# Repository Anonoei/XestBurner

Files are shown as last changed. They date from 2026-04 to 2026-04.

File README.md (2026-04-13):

# XestBurner
A light modular toolhead designed in OpenSCAD

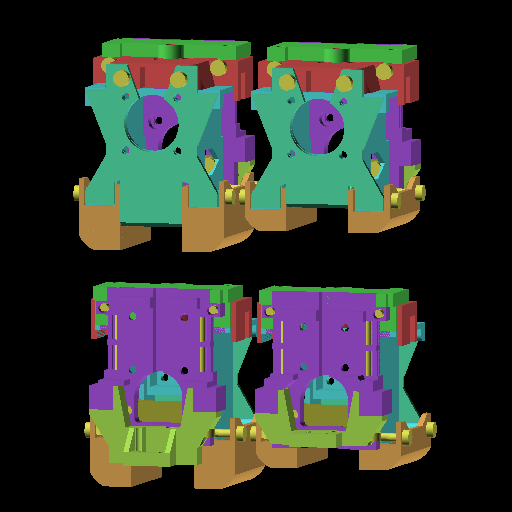
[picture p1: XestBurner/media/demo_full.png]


**This is WORK-IN-PROGRESS**

## Links
- [Description](#description)
- [BOM](#bom)
- [STLs](#stls)
- [Assembly Guide](ASSEMBLY.md)

## Description
XestBurner is meant to be as small as possible, maximizing available print space, while also being modular and allowing components to be switched with minimal tweaks to the toolhead.

XestBurner works with HF (standard, v6) hotends, and UHF (volcano) hotends.

The HF variant measures 61x53x67 (width (x)/depth (y)/height (z)).

### Why?
This toolhead was heavily inspired by the amazing work done for  [Xol](https://github.com/Armchair-Heavy-Industries/Xol-Toolhead), and [Dragonburner](https://github.com/chirpy2605/voron/tree/main/V0/Dragon_Burner)

I switched to a CHUBE hotend, and found that none of the current toolheads supported it, along with features that are necessary, like ease-of-assembly, modular components, and being light.

This toolhead was designed around having a similar footprint to DragonBurner, supporting CHUBE (and other large hotends), and using only M3 hardware.

## BOM
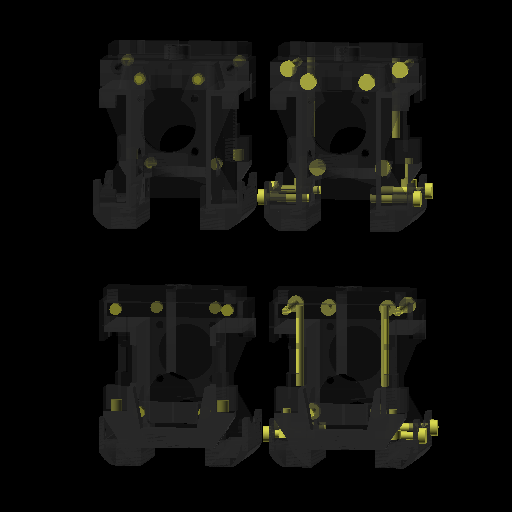
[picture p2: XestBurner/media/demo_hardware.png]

- Prints:
  - Housing
  - Housing Brace
  - Ducts (HF or UHF)
  - [Carriage mount](#carriage)
  - [Hotend mount](#hotend)
  - [Extruder mount](#extruder)
  - [Probe mount](#probe)
  - [Faceplate](#faceplate)
- Hardware:
  - 2x 4010 blower fans (sides of housing)
    - [WINSINN (Amazon)](https://www.amazon.com/WINSINN-Turbine-Brushless-Hydraulic-Extruder/dp/B07L2WTH7H)
    - [West3D BERSERKER VINDR](https://west3d.com/products/berserker-vindr-ulta-performance-4010-blower-fan-24v-4010b-24v-a-40x10mm)
    - [Fabreeko HoneyBadger](https://www.fabreeko.com/products/4010-blower-p-series-fan-by-honeybadger)
    - [KB3D](https://kb-3d.com/store/fans/663-4010-ball-bearing-blower-fan-24v-1662421807065.html)
  - 1x 2510 fan (front of housing)
    - [WINSINN (Amazon)](https://www.amazon.com/WINSINN-Bearings-Brushless-Cooling-25mm10mm/dp/B08R9JXMGP?tag=ustxtaddt-20&th=1)
    - [West3D BERSERKER VINDR](https://west3d.com/products/berserker-vindr-ultra-performance-2510-axial-fan-24v-2510a-24v-a-25x10mm)
    - [Fabreeko HoneyBadger](https://www.fabreeko.com/products/2510-performance-axial-fan-by-honeybadger)
    - [KB3D](https://kb-3d.com/store/fans/3684-2510-ball-bearing-cooling-fan-24v-1740693669311.html)
  - 8x M3x4x5 (Voron) heatsets
    - 6x for carriage, 2 for housing brace, 2 for hotend/extruder, 2 for probe
    - 2x for hotend mount
  - 2x M3x30 pins (inside the carriage for belts)
  - 2x SHCS/BHCS M3x6 (faceplate, into 2x heatsets on the hotend mount)
    - M3x8 probably works
  - 6x SHCS/BHCS M3x8
    - 4x: faceplate, into 2510 fan
    - 2x: probe mount, into 2x heatsets on the bottom of the carriage
  - 4x SHCS M3x16 (housing ducts, through the 4010 fans)
  - 2x SHCS M3x30 (hotend mount, into 2x heatsets on the front of the carriage)
- Variants
  - Carriage
    - MGN12H
      - 4x SHCS M3x8 (?)
    - MGN9H
      - 4x SHCS M3x8 (?)
  - Extruder
    - Sherpa Mini
      - 2x M3x4x5 heatsets
      - 2x SHCS M3x8 (?)
  - Probe
    - Klicky PCB
      - 3x M2.5 heatsets

## STLs
### Base
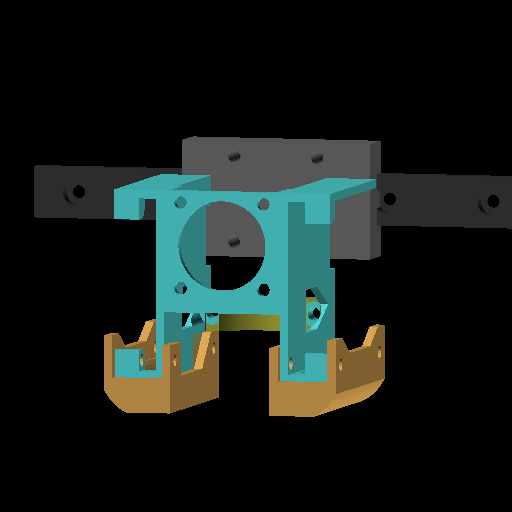
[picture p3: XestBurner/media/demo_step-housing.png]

- [Housing](XestBurner/STLs/XB-housing.stl)
- [Housing: Brace](XestBurner/STLs/XB-housing_brace.stl)
- Ducts:
  - [HF](XestBurner/STLs/XB-ducts-hf.stl)
  - [UHF](XestBurner/STLs/XB-ducts-uhf.stl)

### Carriage
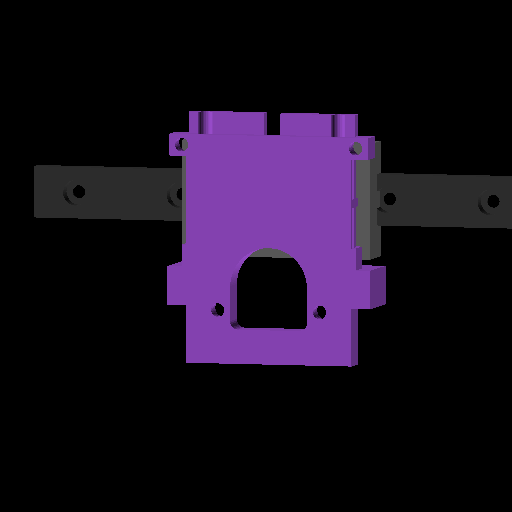
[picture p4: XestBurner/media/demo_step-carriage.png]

- [MGN9H](XestBurner/STLs/XB-carriage_MGN9.stl)
- [MGN12H](XestBurner/STLs/XB-carriage_MGN12.stl)

### Hotend
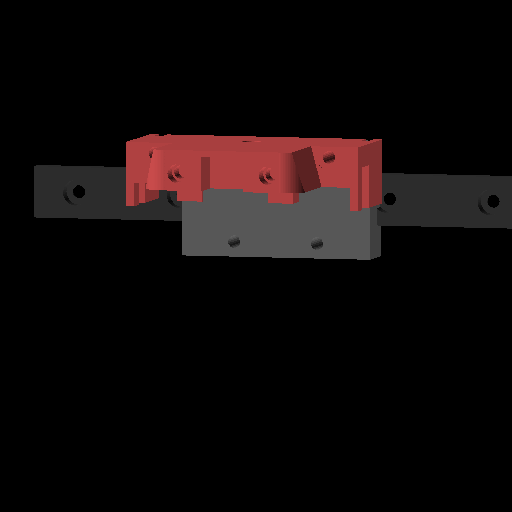
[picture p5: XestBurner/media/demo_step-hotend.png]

- [Phaetus Rapido](XestBurner/STLs/XB-hotend_phaetus-rapido.stl)
- [Chube](XestBurner/STLs/XB-hotend_chube.stl)
- [Phaetus Dragonfly BMO](XestBurner/STLs/XB-hotend_phaetus-dragonfly-bmo.stl)

### Extruder
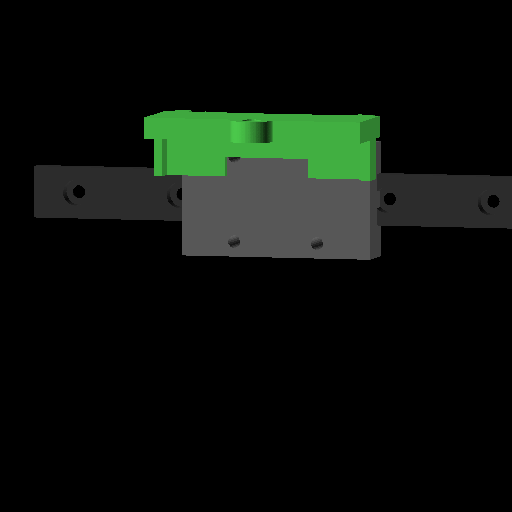
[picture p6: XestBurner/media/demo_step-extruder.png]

- [Sherpa Mini](XestBurner/STLs/XB-extruder_sherpa-mini.stl)

### Probe
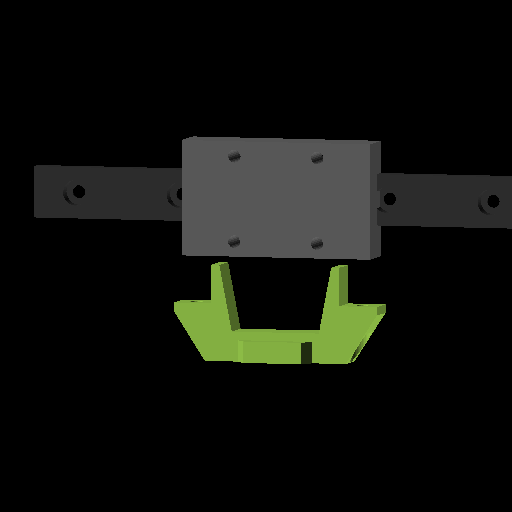
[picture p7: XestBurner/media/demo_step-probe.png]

#### HF
- [Klicky PCB](XestBurner/STLs/XB-probe-hf_klicky-pcb.stl)
#### UHF
- [Klicky PCB](XestBurner/STLs/XB-probe-uhf_klicky-pcb.stl)

### Faceplate
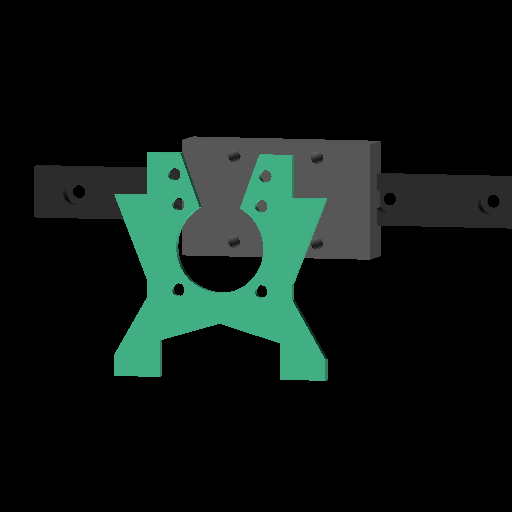
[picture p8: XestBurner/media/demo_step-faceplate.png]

- [Standard](XestBurner/STLs/XB-faceplate.stl)
#### HF
- [LEDs](XestBurner/STLs/XB-faceplate-hf_led.stl)
- [LEDs and nozzle cam](XestBurner/STLs/XB-faceplate-hf_led_cam.stl)
#### UHF
- [LEDs](XestBurner/STLs/XB-faceplate-uhf_led.stl)
- [LEDs and nozzle cam](XestBurner/STLs/XB-faceplate-uhf_led_cam.stl)

## Development
### Export STLs
- run `python3 scadboil/run.py -p XestBurner -a export`
### Export images
- run `python3 scadboil/run.py -p XestBurner -a image`

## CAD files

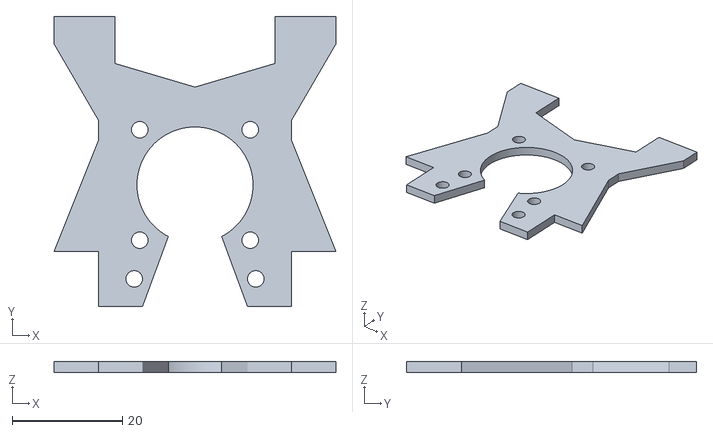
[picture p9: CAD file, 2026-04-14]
XestBurner/STLs/XB-faceplate.stl
51.0 x 52.5 x 2.00

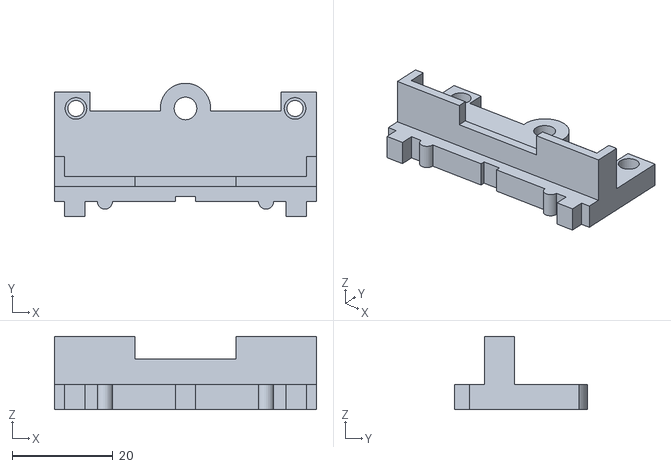
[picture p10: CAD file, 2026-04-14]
XestBurner/STLs/XB-extruder_sherpa-mini.stl
52.0 x 26.5 x 14.5

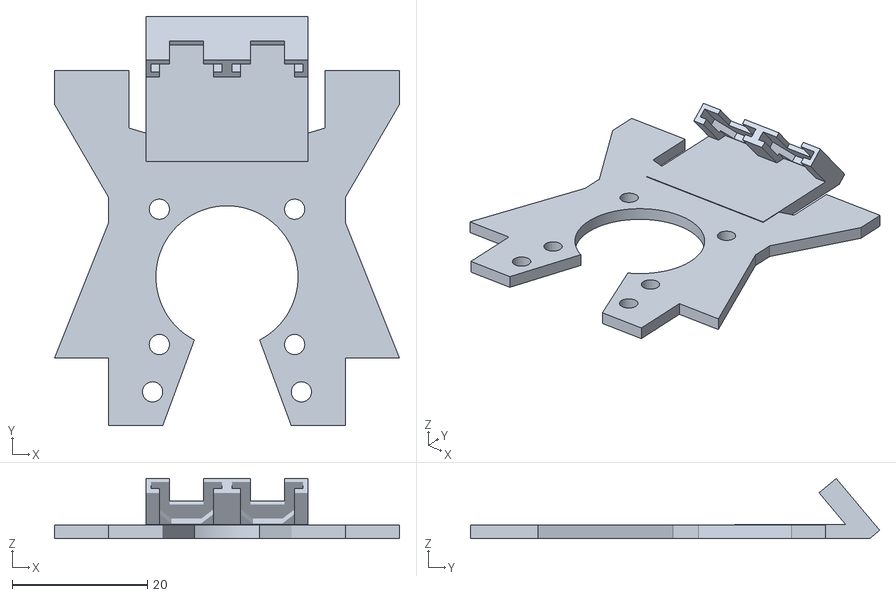
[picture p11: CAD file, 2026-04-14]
XestBurner/STLs/XB-faceplate-uhf_led.stl
51.0 x 60.5 x 8.89

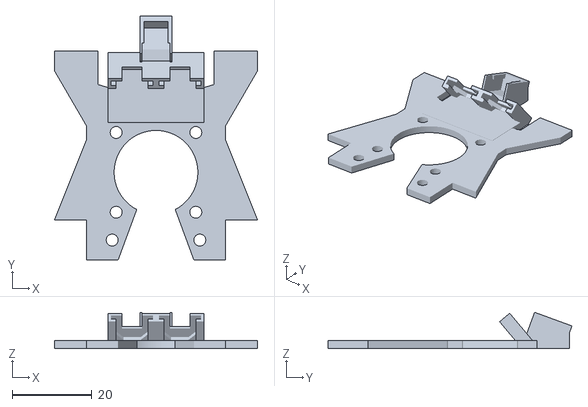
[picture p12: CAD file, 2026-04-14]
XestBurner/STLs/XB-faceplate-hf_led_cam.stl
51.0 x 61.2 x 9.13

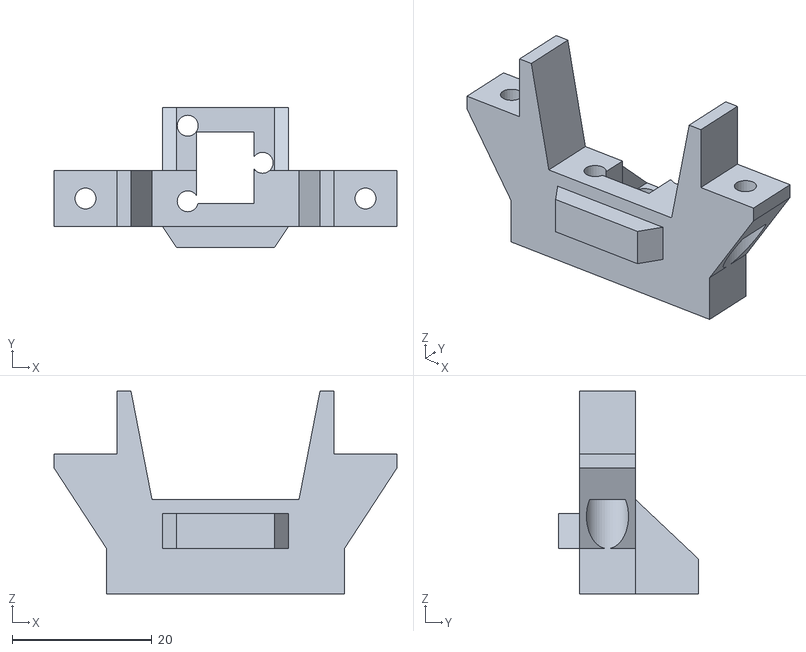
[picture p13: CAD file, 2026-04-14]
XestBurner/STLs/XB-probe-uhf_klicky-pcb.stl
49.0 x 20.0 x 29.0

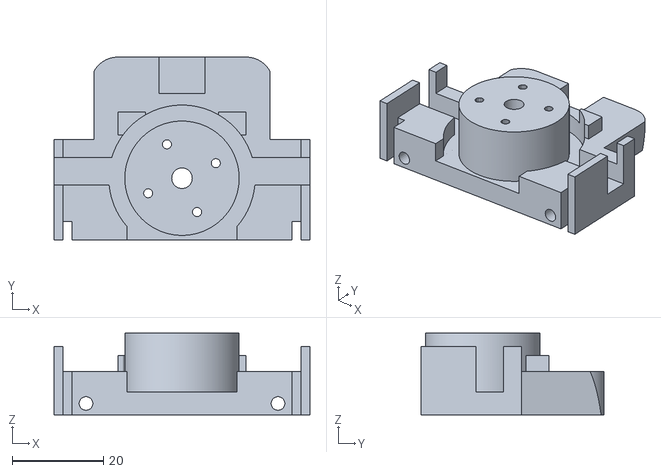
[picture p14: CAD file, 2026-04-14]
XestBurner/STLs/XB-hotend_phaetus-dragonfly-bmo.stl
56.0 x 40.0 x 17.9

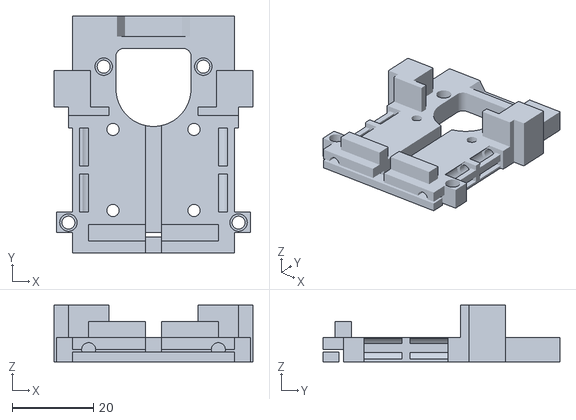
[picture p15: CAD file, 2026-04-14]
XestBurner/STLs/XB-carriage_MGN12.stl
49.0 x 58.5 x 14.0

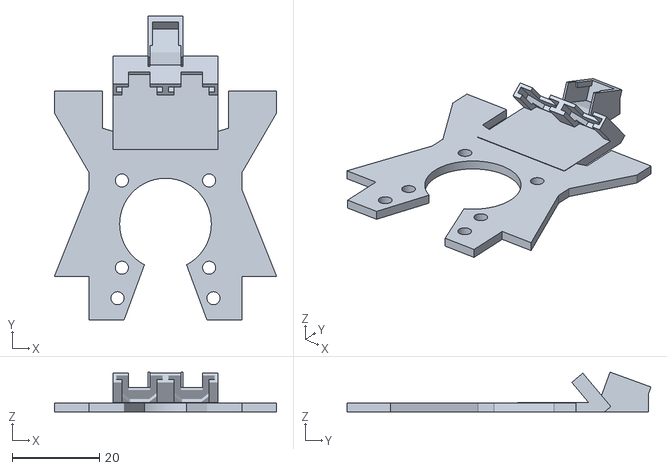
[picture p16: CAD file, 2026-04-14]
XestBurner/STLs/XB-faceplate-uhf_led_cam.stl
51.0 x 69.7 x 9.13

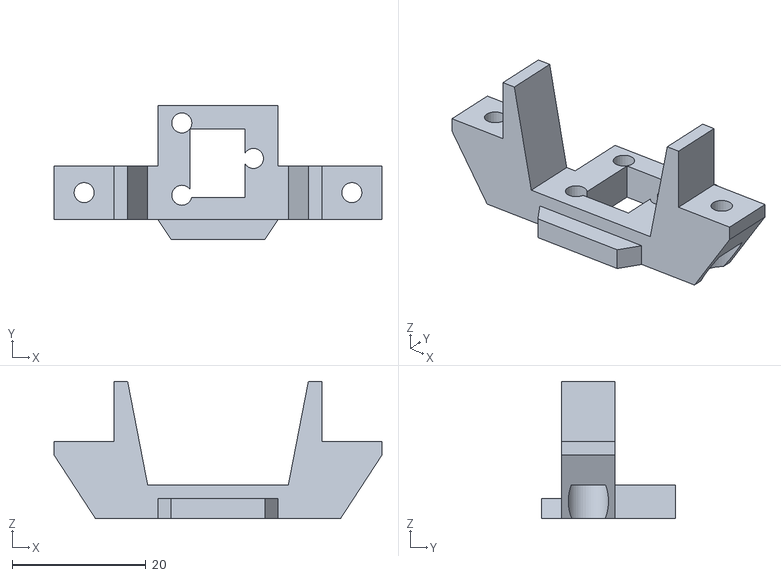
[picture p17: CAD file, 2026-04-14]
XestBurner/STLs/XB-probe-hf_klicky-pcb.stl
49.0 x 20.0 x 20.5

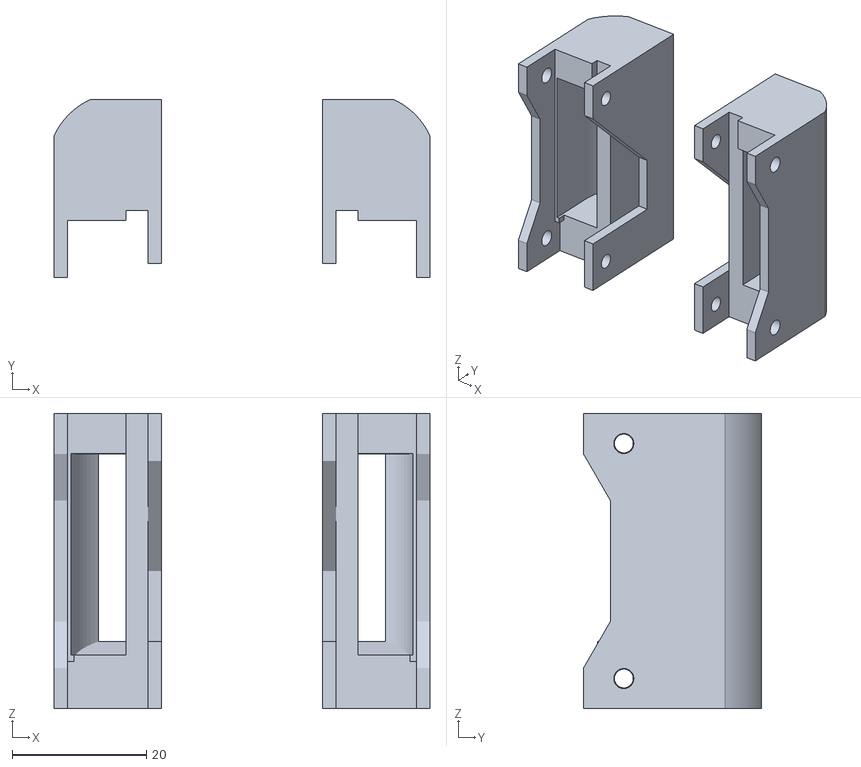
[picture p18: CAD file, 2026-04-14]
XestBurner/STLs/XB-ducts-uhf.stl
56.0 x 26.5 x 44.0

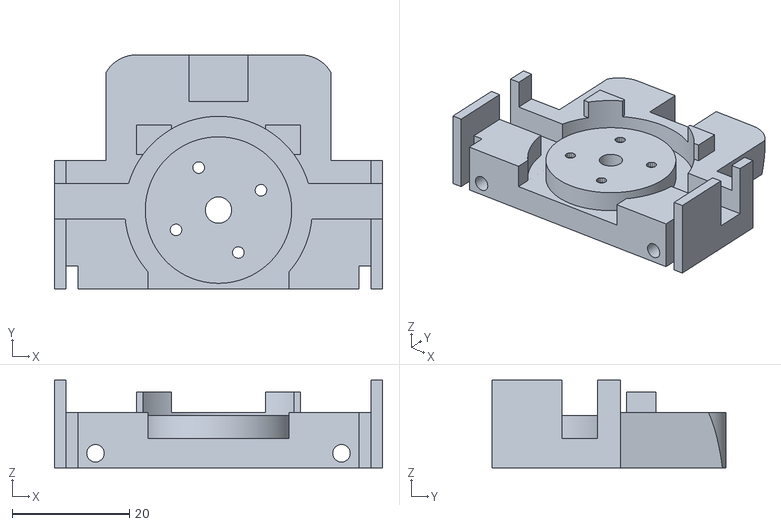
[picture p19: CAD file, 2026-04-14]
XestBurner/STLs/XB-hotend_phaetus-rapido.stl
56.0 x 40.0 x 15.0

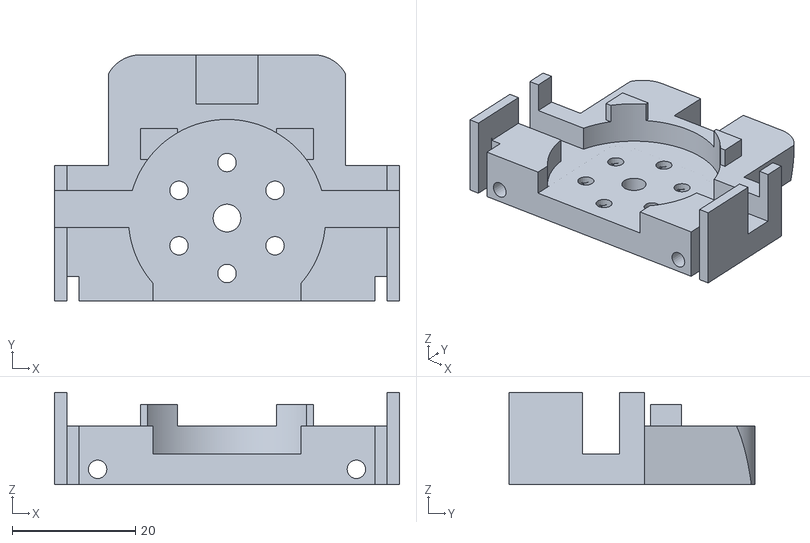
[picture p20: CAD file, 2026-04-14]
XestBurner/STLs/XB-hotend_chube.stl
56.0 x 40.0 x 15.0

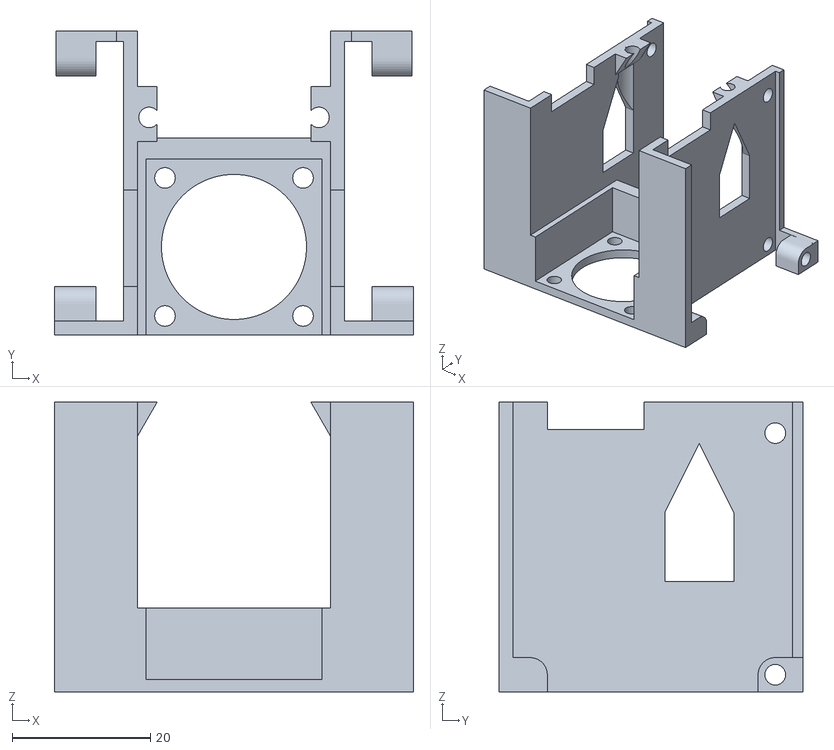
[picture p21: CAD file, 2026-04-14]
XestBurner/STLs/XB-housing.stl
52.0 x 44.0 x 42.0

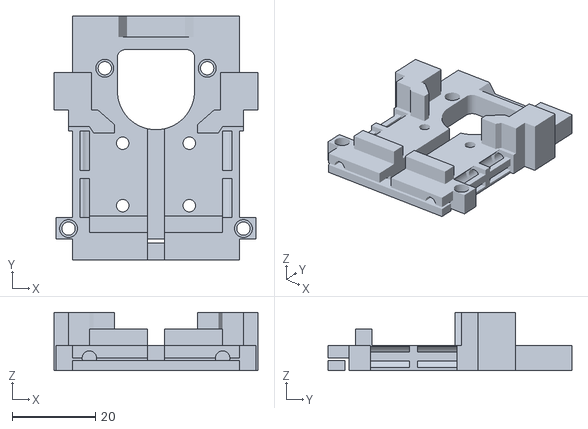
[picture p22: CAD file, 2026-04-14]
XestBurner/STLs/XB-carriage_MGN9.stl
49.0 x 58.5 x 14.0

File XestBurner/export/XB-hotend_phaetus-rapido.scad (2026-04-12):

include <../src/main.scad>

rotate([180,0,0])
xb_he_rapido();

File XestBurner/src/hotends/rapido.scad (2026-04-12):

module xb_he_rapido() {
    module _mount() {
        translate([0,d_he_c,d_he_hf])
            ven_hotend_phaetus_rapido(true,he=20);
        translate([0,d_he_c,-5])
            cylinder(d=4.5,h=60);
    }
    module _base() {
        union() {
            xb_he();
            translate([0,d_he_c,6.5+0.01])
                cylinder(d=25,h=5);
        }
    }
    difference() {
        _base();
        _mount();
    }
}

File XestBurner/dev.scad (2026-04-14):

include <src/main.scad>

include <src/bounds.scad>

include <_demo_utils.scad>

module measure_check() {
    bound_w = d_max_w+5;
    bound_h = d_max_h+2;
    bound_d = d_max_d+3;
    translate([-bound_w/2, -bound_d, -46.5])
        color([0.5, 0.1, 0.1, 0.5]) cube([bound_w, bound_d, bound_h]);

    echo("Bounds: width ", bound_w, ", depth: ", bound_d, ", height: ", bound_h);
}

module he_rapido() {
    translate([0,d_he_c,d_he_hf])
    rotate([0,0,90])
        color([0.8,0.1,0.1,0.5]) ven_hotend_phaetus_rapido();
}

module he_chube() {
    translate([0,d_he_c,d_he_uhf])
    rotate([0,0,90])
        color([0.8,0.1,0.1,0.5]) ven_hotend_chube();
}

module xb_base() {
    // Housing
    color(c_cl) xb_fh();
    color(c_y) xb_fh_brace();
    color(c_ol) xb_du_hf();
    // Carriage
    color(c_pl) xb_cr();
    // Hotend
    color(c_rl) xb_he();
    // // Extruder
    color(c_gl) xb_em();
    // // Probe
    color(c_ll) xb_pr();
    // // Faceplate
    color(c_sl) xb_fp();

    xb_hardware();
}

module xb_hf_var1() {
    // Housing
    color(c_cl) xb_fh();
    color(c_y) xb_fh_brace();
    color(c_ol) xb_du_hf();
    // Carriage
    color(c_pl) xb_cr_mgn9h();
    // color(c_pl) xb_cr_mgn12h();
    // mgn9();
    // Hotend
    color(c_rl) xb_he_rapido();
    // Extruder
    // color(c_gl) xb_em_sherpa_mini();
    // Probe
    // color(c_ll) xb_pr_klicky_pcb_hf();
    // Faceplate
    // color(c_sl) xb_fp();

    // xb_b_hf();
    // xb_hardware();
    // xb_heatsets();
    // color(c_yl) xb_cr_mgn12h_bolts();

    // xb_fh_bolt_cut();
}

module demo_uhf_var1() {
    // Housing
    color(c_cl) xb_fh();
    color(c_y) xb_fh_brace();
    color(c_ol) xb_du_uhf();
    // Carriage
    color(c_pl) xb_cr_mgn12h();
    // mgn12();
    // Hotend
    color(c_rl) xb_he_rapido();
    // Extruder
    color(c_gl) xb_em_sherpa_mini();
    // // Probe
    color(c_ll) xb_pr_klicky_pcb_uhf();
    // // Faceplate
    color(c_sl) xb_fp();
    // xb_fp_led_uhf();

    xb_b_uhf();

    xb_hardware();
    // xb_heatsets();
    // color(c_yl) xb_cr_mgn12h_bolts();
}





// xb_base();
xb_hf_var1();
// demo_uhf_var1();

he_rapido();

// xb_hardware();
// xb_heatsets();

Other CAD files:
XestBurner/STLs/XB-faceplate-hf_led.stl
XestBurner/STLs/XB-housing_brace.stl
XestBurner/STLs/XB-ducts-hf.stl
XestBurner/export/XB-carriage_MGN12.scad
XestBurner/_demo_mercury.scad
XestBurner/_demo_palladium.scad
XestBurner/_demo_utils.scad
XestBurner/demo.scad
XestBurner/demo_assembly-1carriage_pins.scad
XestBurner/demo_assembly-1heatsets_carriage.scad
XestBurner/demo_assembly-1heatsets_hotend.scad
XestBurner/demo_assembly-1supports_carriage.scad
XestBurner/demo_assembly-2housing.scad
XestBurner/demo_assembly-2housing_brace.scad
XestBurner/demo_assembly-2housing_ducts.scad
XestBurner/demo_assembly-3hotend.scad
XestBurner/demo_assembly-3hotend_extruder.scad
XestBurner/demo_assembly-4probe.scad
XestBurner/demo_assembly-5housing_carriage.scad
XestBurner/demo_assembly-5housing_hotend.scad
XestBurner/demo_full.scad
XestBurner/demo_hardware.scad
XestBurner/demo_step-carriage.scad
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

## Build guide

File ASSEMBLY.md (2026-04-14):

# Assembly

**This is WORK-IN-PROGRESS**

## Initial Assembly

### Prereqs
1. Remove supports
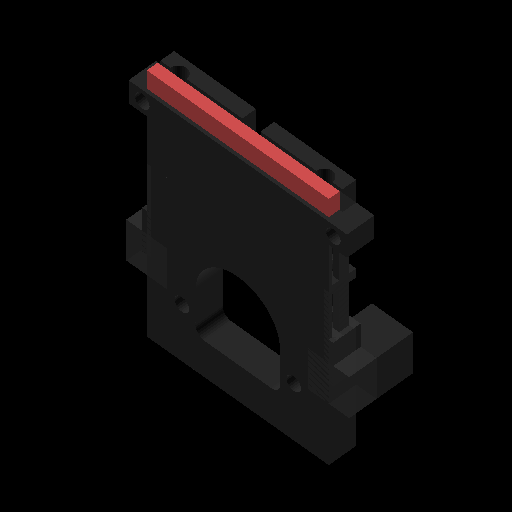
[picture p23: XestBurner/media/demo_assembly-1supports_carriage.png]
   - Carriage
2. Install heatsets
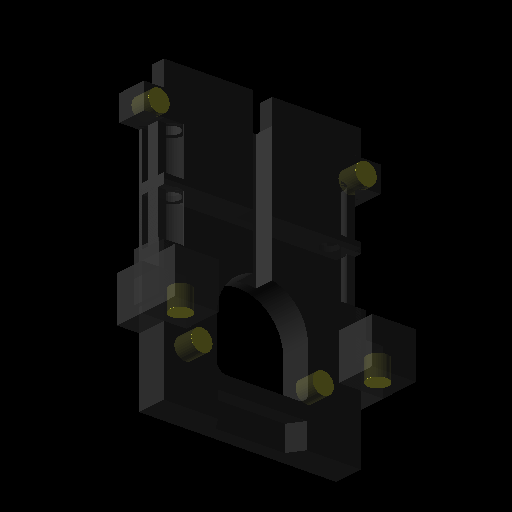
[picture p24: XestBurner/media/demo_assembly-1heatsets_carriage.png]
   - Carriage: 
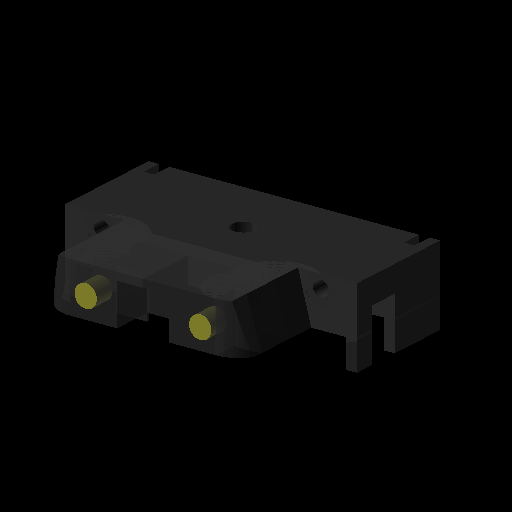
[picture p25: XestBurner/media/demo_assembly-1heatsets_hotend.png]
   - Hotend mount: 
3. If needed, install additional heatsets into variants
4. Install specific components
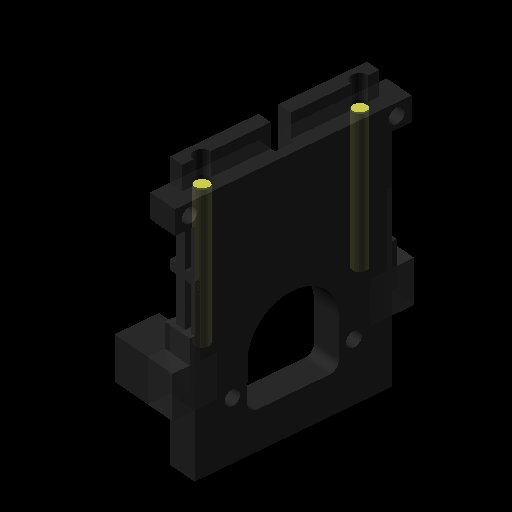
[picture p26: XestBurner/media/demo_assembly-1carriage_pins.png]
   - Insert 2x M3x30 pins into the carriage, from the top

### Housing
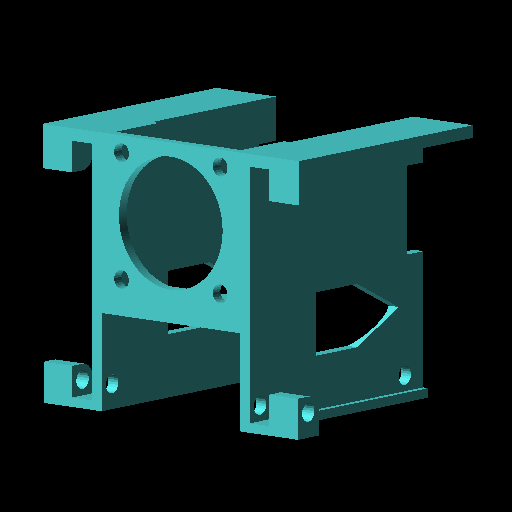
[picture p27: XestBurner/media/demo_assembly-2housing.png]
1. Install 4010 blower fans 
   - Push 4010 fan cables through the slot in the housing
   - The fans will mostly press-fit in place. Ensure the open side of the fan is facing down, with the arrow pointing away from the side of the housing that's solid.
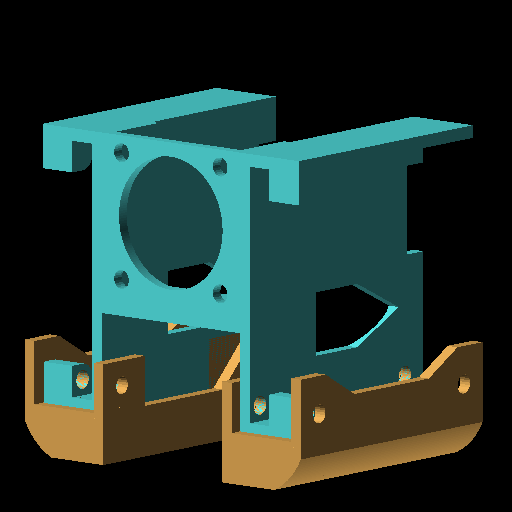
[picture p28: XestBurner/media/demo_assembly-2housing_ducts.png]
2. Press-fit ducts 
   - Slide the ducts over the housing and 4010 fans
3. Put 2x M3x16 into each duct, with the bolts going through the holes in the fan
   - **These screw into plastic, be gentle**
4. Press the 2510 fan into the front of the housing

### Hotend/extruder
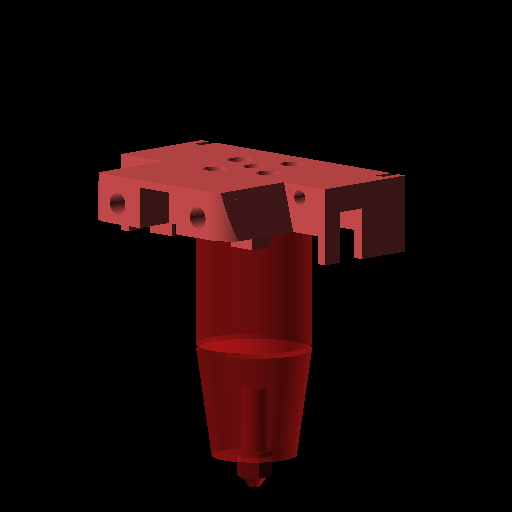
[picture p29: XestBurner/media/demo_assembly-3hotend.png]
1. Bolt hotend to mount 
   - Try to make the cables face towards the back to make cable routing easier
2. Bolt extruder to mount
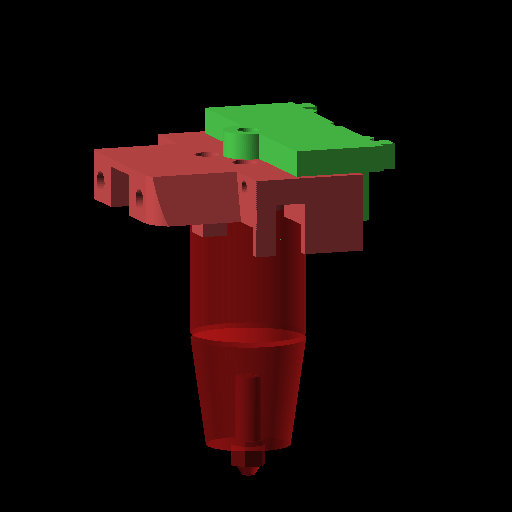
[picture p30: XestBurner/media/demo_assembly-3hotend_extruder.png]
3. Connect hotend and extruder mount 
   - Press fit from the back of the hotend mount

### Carriage
1. Assemble your probe
2. Attach probe mount to carriage
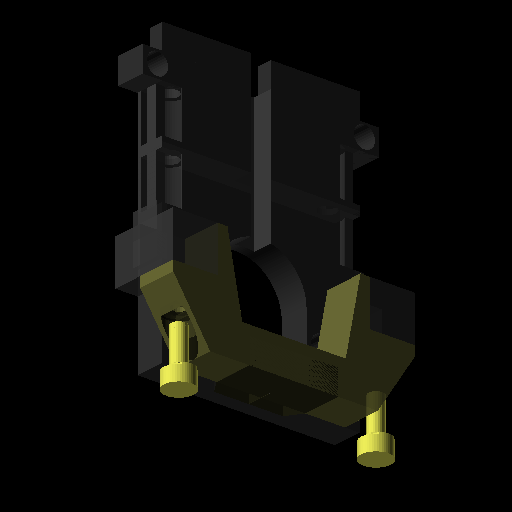
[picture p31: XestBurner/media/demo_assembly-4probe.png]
   - 
3. Pull your belts, and push them through the slots on the carriage.
   1. The belts will go around the M3 pins, and come out the other side.
   2. After putting all 4 belts through, bolt the carriage mount onto the linear rail, and pull the belts tight

### Bring it together
1. Attach housing to the carriage
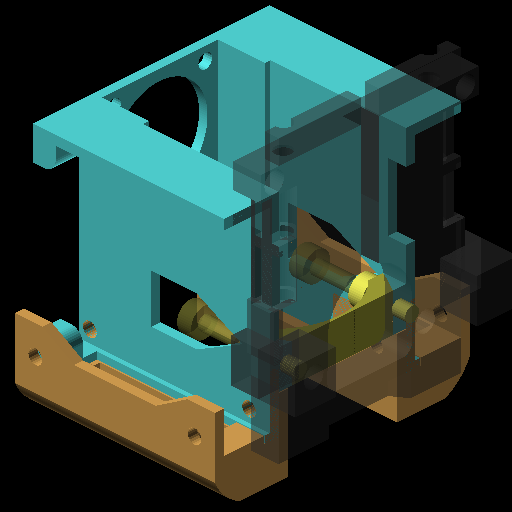
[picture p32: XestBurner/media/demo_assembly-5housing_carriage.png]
   - 
   - Put 2x M3x8 bolts through the housing brace, through the housing, and into the 2x heatsets in the carriage
     - It may help to lightly thread the bolts through the brace and into the housing prior to trying to attach to the carriage
2. Attach hotend/extruder mounts to the carriage
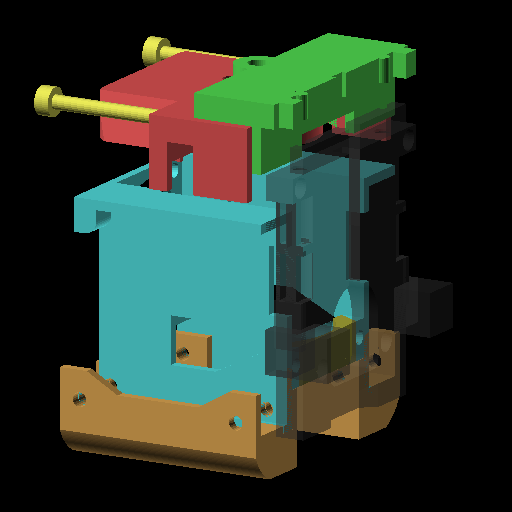
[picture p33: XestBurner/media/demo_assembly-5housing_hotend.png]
   - 
   -  Press the hotend/extruder mounts onto the top of the housing
   -  Route the fan cables to either side through the holes in the hotend mount
4. Put the two M3x30 bolts through the hotend mount, through the extruder mount, and into the 2 heatsets on the carriage
5. Run the hotend cable through the hole near the bottom of the carriage, and up the channel towards the extruder
6. Attach the faceplate

## Swapping parts
- Swap/Reprint fan housing
  1. Release fan wires
  2. Undo 2x M3 bolts
  3. Pull fan housing off
- Swap/reprint hotend
  1. Release hotend wires
  2. Undo 2x M3 bolts
  3. Lift extruder out of the way
  4. Pull hotend out

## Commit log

2026-04-12 Add XestBurner
    [XB-carriage_MGN12.scad, XB-carriage_MGN12.stl, XB-carriage_MGN9.scad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]
2026-04-12 Update README, tweak export naming
    [XB-carriage_MGN12.stl, XB-carriage_MGN9.stl, XB-ducts-hf.scad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]
2026-04-12 Add multiple demos
    [_demo_utils.scad, demo_full.scad, demo_step-carriage.scad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]
2026-04-12 Update demos, switch to orthogonal view
    [_demo_mercury.scad, _demo_palladium.scad, demo_full.scad]
2026-04-13 Add BOM to README, create dev.scad
    [demo_full.scad, dev.scad]
2026-04-13 fix MGN12H btm_press
    [mgn12h.scad]
2026-04-13 Add visualizations for all bolts and heatsets. Export images
    [_demo_utils.scad, carriage.scad, demo_hardware.scad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]
2026-04-13 Clean up BOM, re-export
    [XB-carriage_MGN12.stl, XB-carriage_MGN9.stl, XB-ducts-hf.stl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]
2026-04-14 Tweak housing brace angle, clean up bolt cuts
    [housing.scad]
2026-04-14 Clean up MGN9H bottom press
    [mgn9h.scad]
2026-04-14 Export and image
    [XB-carriage_MGN12.stl, XB-carriage_MGN9.stl, XB-ducts-hf.stl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]
2026-04-14 Fix housing bolt being slightly offset from carriage
    [housing.scad]
2026-04-14 Add housing brace assembly image, export STLs
    [XB-carriage_MGN12.stl, XB-carriage_MGN9.stl, XB-ducts-hf.stl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]
2026-04-14 Clean up carriage supports
    [XB-carriage_MGN12.scad, XB-carriage_MGN12.stl, XB-carriage_MGN9.scad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]
2026-04-14 Add 0.2 tolerance to housing/duct
    [housing.scad]
2026-04-14 Update exports
    [XB-carriage_MGN12.stl, XB-carriage_MGN9.stl, XB-ducts-hf.stl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]
